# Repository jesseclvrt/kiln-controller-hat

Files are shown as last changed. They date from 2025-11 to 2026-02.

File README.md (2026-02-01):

# Kiln Controller HATs
HATs to implement [jbruce12000/kiln-controller](https://github.com/jbruce12000/kiln-controller) in Raspberry Pi Zero W form-factor.

## Two PCBs
There are two PCBs for controlling the MAX31855 in either software (right) or hardware(left) SPI. The software PCB has a cleaner layout with traces, but is allegedy slower.

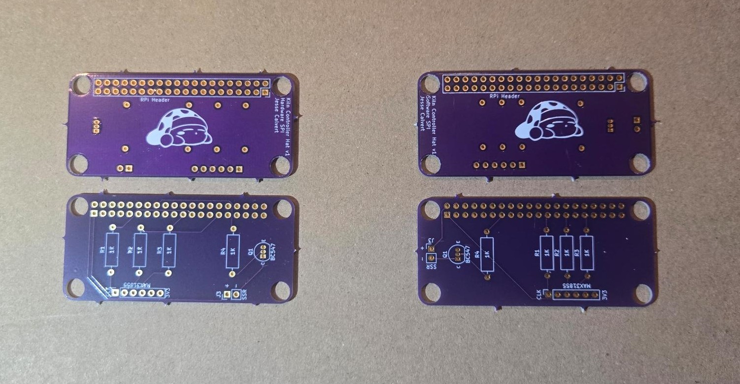
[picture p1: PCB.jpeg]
PCBs


## BOM
In addition to the regular materials for jbruce12000's controller, you will need:

* 1x6 socket header with 2.54mm pitch (MAX31855)
* 2x20 socket header with 2.54mm pitch (RPi GPIO)
* 1x2 pin or socket header with 2.54 pitch (SSR)

## Assembly
Ensure the GPIO header gets soldered to the back of the board. Solder in the resistors, transistor, and socket headers. The hat is attached to use the entire GPIO header, although it only uses a small number of pins.

The MAX31855 is attached upside down onto the board. This is because I already soldered my pins rightside up and I didn't want to resolder or buy a new MAX. The design would need to be changed to flip the MAX header around for a cleaner looking install.

Remember to update your config.py to reflect which pins you are using. Hardware SPI should define no pins. The software SPI board uses these pins:

| Physical Pin | GPIO | Connected to | config.py line |
| --- | ---- | --- |---|
| 23 | 11 | MAX31855 CLK | spi_sclk = board.D11  |
| 27 | 0 | MAX31855 CS  | spi_cs = board.D0 |
| 31 | 6 | MAX31855 DO  | spi_miso = board.D6 |
| 13 | 27 | SSR Control  | gpio_heat = board.D27 |

Set spi_mosi (serial input) to any unused pin, such as D10.

The board has the same dimensions as the Raspberry Pi Zero W, because that's the device I happened to have for this project. Drill holes are aligned to match that device, so maybe someone could make a nice 3D printed case for the whole assembly. Due to this, the board does have a lot of unused space, so the design can also be adjusted to save some manufacturing cost. Alternatively, maybe some additional features could be added, although I don't have the electronics skill for that.

## Thanks
Thank you [jbruce12000](https://github.com/jbruce12000) for reviving dead analog kilns with Raspberry Pi magic, and [Tech Explorations](https://techexplorations.com/) for teaching me the basics of KiCAD. These are my first PCB designs, so feedback would be welcome.

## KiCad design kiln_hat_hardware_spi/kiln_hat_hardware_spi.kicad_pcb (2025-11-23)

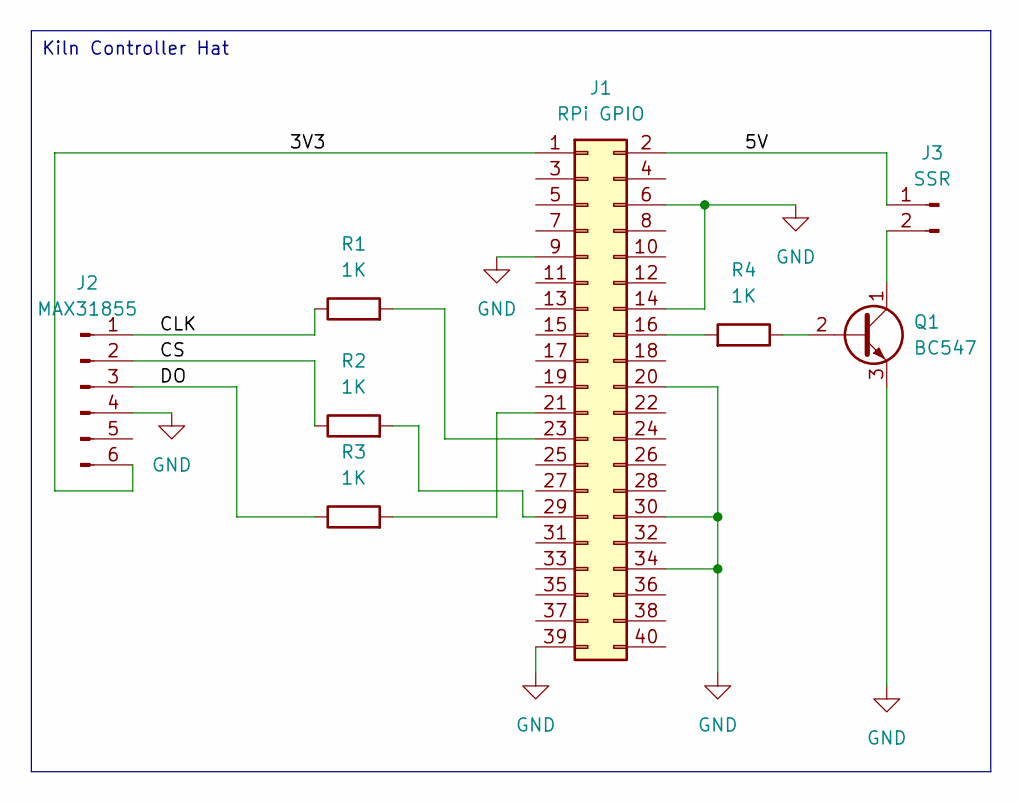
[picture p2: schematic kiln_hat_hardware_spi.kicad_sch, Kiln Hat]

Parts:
J1: RPi GPIO; PinSocket_2x20_P2.54mm_Vertical
J2: MAX31855; PinSocket_1x06_P2.54mm_Vertical
J3: SSR; PinHeader_1x02_P2.54mm_Vertical
Q1: BC547; TO-92_Inline
R1, R2, R3, R4: 1K; R_Axial_DIN0309_L9.0mm_D3.2mm_P12.70mm_Horizontal

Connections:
/3V3: J1.1, J2.6
/5V: J1.2, J3.1
/CLK: J2.1, R1.1
/CS: J2.2, R2.1
/DO: J2.3, R3.1
GND: J1.6, J1.9, J1.14, J1.20, J1.30, J1.34, J1.39, J2.4, Q1.3 (E)
unnamed: J1.16, R4.2
unnamed: J1.21, R3.2
unnamed: J1.23, R1.2
unnamed: J1.29, R2.2
unnamed: J3.2, Q1.1 (C)
unnamed: Q1.2 (B), R4.1

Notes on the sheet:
Kiln Controller Hat

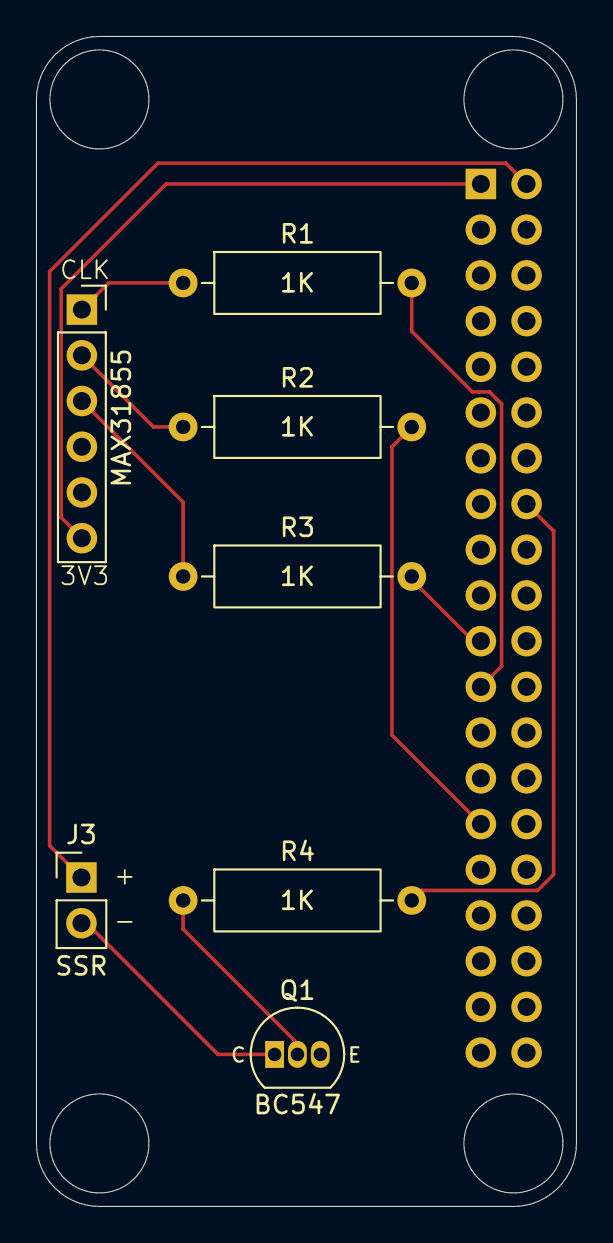
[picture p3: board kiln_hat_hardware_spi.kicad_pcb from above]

Board: 2 copper layers, 30.0 x 65.0 mm, 8 parts (1 on the bottom side), 12 nets.

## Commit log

2026-02-01 Delete kiln_hat_hardware_spi/gerbers.zip
    moved to releases
2026-02-01 Delete kiln_hat_software_spi/gerbers.zip
    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
2026-02-01 updating readme with image of PCBs and links to special mentions
